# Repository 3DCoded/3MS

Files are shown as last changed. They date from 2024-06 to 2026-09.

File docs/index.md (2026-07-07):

---
title: 3MS Home
icon: material/home
---

# Welcome to the 3MS Documentation

The 3MS is short for MMMS, which stands for **M**odular **M**ulti **M**aterial **S**ystem

(https://www.printables.com/model/1108644-beta-3home-3ms-hybrid-official-modular-enclosure)

[Configuration Generator](https://forked-lined-hour.anvil.app/)

Discord Shield (https://discord.gg/ekqxDhdGCg)

The 3MS is a simple, compact, modular, reliable, budget-friendly multimaterial system.

[Get Started :material-format-list-numbered:](instructions/index.md){ .md-button }

## Why 3MS?

Why use the 3MS when there are many other multi-material systems?

Here are a few reasons:

- **Simplified Design**: Minimal mechanical complexity for increased reliability.
- **Low Cost**: A 4-filament-unit 3MS can be built for ~$150 USD
- **Easily Sourceable**: All the parts for the 3MS are available on Amazon. Alternatively, you can purchase a 3MS kit from West3D.
- **Comprehensive Documentation**: Step-by-step guides to ensure smooth setup and operation.
- **Scalable**: Easily expand the system to handle any number of filaments.

## Requirements

To use the 3MS, your setup should meet the following requirements:

- Run ^^legit^^ Klipper firmware. Most printers that come with Klipper preinstalled use a ^^modified^^ version of Klipper and/or Linux that will impact your ability to setup Happy Hare firmware. [Read more](https://klipper.discourse.group/t/3d-printers-with-preinstalled-and-modified-klipper-versions/20467?u=3dcoded)
- Have SSH (PuTTY) access (99.9% of Klipper installations have this, and if you don't you really should setup SSH).
- Have one spare USB port.
- Have an adapter to install a PTFE tube to the inlet of your printer's extruder.
- Have one filament sensor right before your printer's extruder.
- Have a filament cutter (ideally between your printer's extruder and hotend). Alternatively, you can use [IF-Cut](https://www.printables.com/model/1417085-beta-if-cut-inline-filament-cutter-for-the-3ms).

## Recommendations

It is recommended to install a filament cutter to your printer to avoid the need to tune tip forming.

## Get Started

To get started with the 3MS, see the [Master Instructions](instructions/index.md).

[Get Started :material-format-list-numbered:](instructions/index.md){ .md-button }

<iframe width="560" height="315"  src="https://www.youtube.com/embed/p-0RshsVmOk?si=rx554jrZFm6iZ0TR" title="YouTube video player" frameborder="0" allow="accelerometer; autoplay; clipboard-write; encrypted-media; gyroscope; picture-in-picture; web-share" referrerpolicy="strict-origin-when-cross-origin" allowfullscreen></iframe>

---

??? "Sample Prints"
    === "T-Rex"
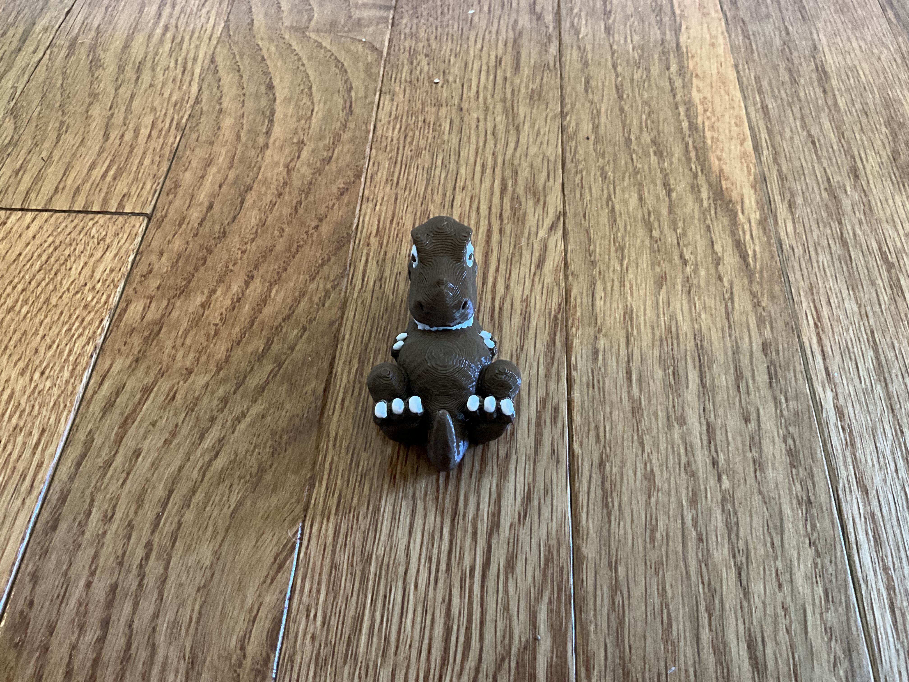
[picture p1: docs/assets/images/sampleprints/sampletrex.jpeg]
        

        Printed at 50% scale

        Model: [T-rex by Cipis](https://www.printables.com/model/5481-t-rex-multi-material)
    === "Lizard"
        

        Model: [Striped lizard with pupils by EngMike](https://www.printables.com/model/236193-striped-lizard-multi-material-with-pupils)
    === "Sheep"
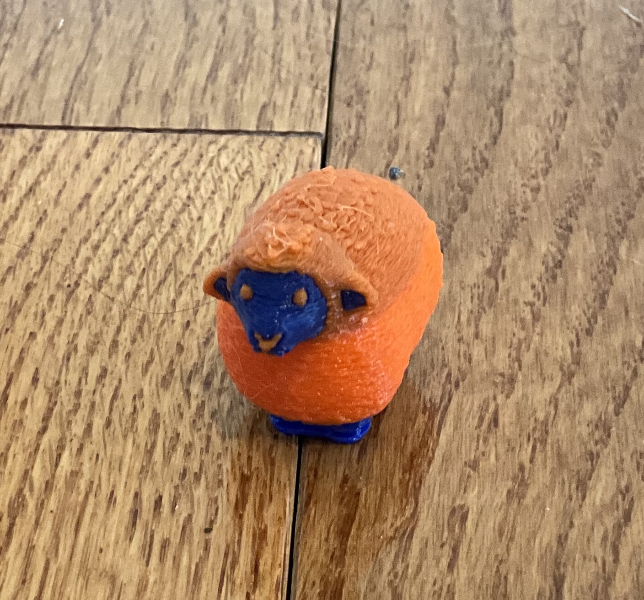
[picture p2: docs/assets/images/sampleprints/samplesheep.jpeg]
        

        Model: [Sheep by Cipis](https://www.printables.com/model/838872-sheep-multi-material-remix)
    === "Calendar"
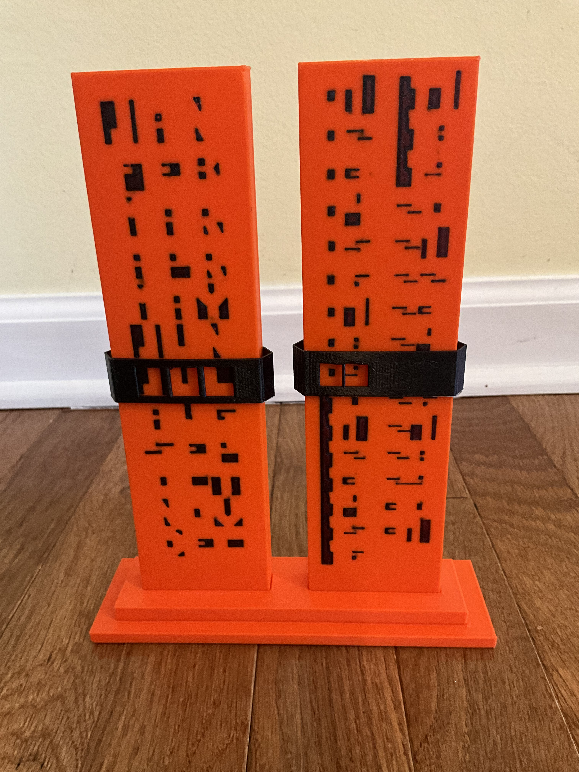
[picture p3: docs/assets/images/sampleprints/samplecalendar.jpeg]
        

        Model: [Monolith Cryptic Calendar by Sevro](https://www.printables.com/model/698341-monolith-cryptic-calendar)
    === "Voron Cube"
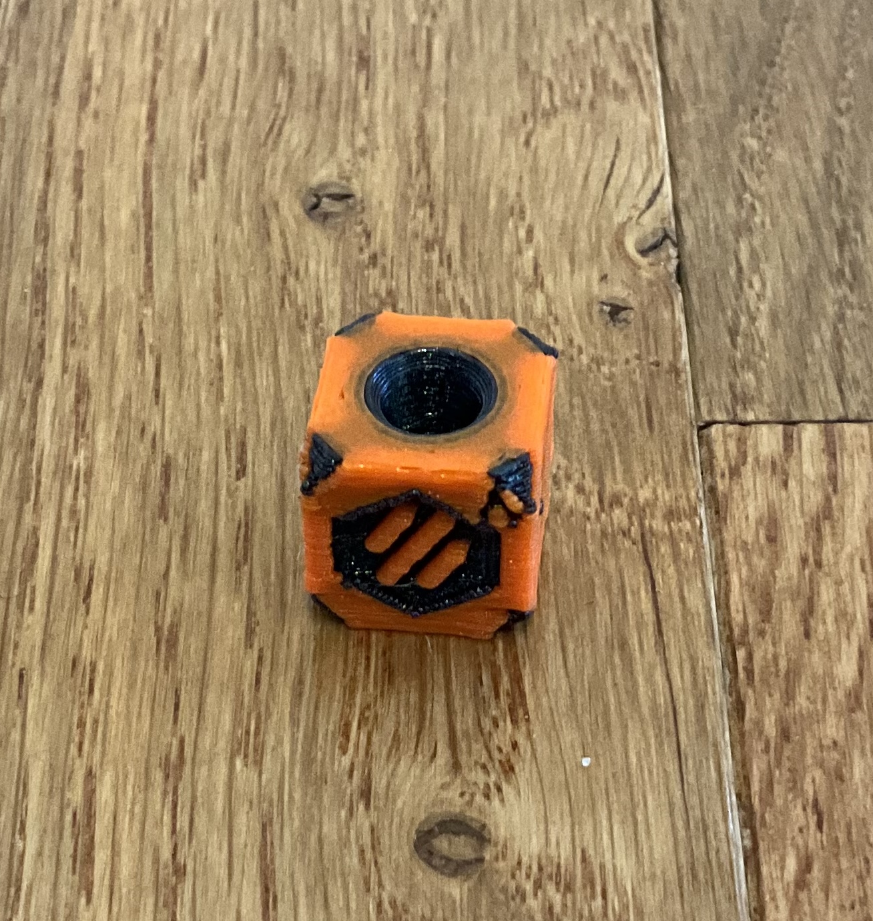
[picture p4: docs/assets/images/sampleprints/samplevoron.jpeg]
        

        Model: Voron Cube (bundled with OrcaSlicer), painted by me in OrcaSlicer

??? "West3D Video Series"
    Thank you to Allen Rowand from [West3D](https://west3d.com/) for making this ongoing series on the 3MS.

    <iframe width="560" height="315" src="https://www.youtube.com/embed/XfjHtymdHao?si=cHG1jreb8FfjpWaL" title="YouTube video player" frameborder="0" allow="accelerometer; autoplay; clipboard-write; encrypted-media; gyroscope; picture-in-picture; web-share" referrerpolicy="strict-origin-when-cross-origin" allowfullscreen></iframe>

    <iframe width="560" height="315" src="https://www.youtube.com/embed/o4Fvtdl-XjM?si=16Prr2Djn4XP0n6q" title="YouTube video player" frameborder="0" allow="accelerometer; autoplay; clipboard-write; encrypted-media; gyroscope; picture-in-picture; web-share" referrerpolicy="strict-origin-when-cross-origin" allowfullscreen></iframe>

    <iframe width="560" height="315" src="https://www.youtube.com/embed/Ndw14nttqQs?si=JtjTmIGCPrT_j4LV" title="YouTube video player" frameborder="0" allow="accelerometer; autoplay; clipboard-write; encrypted-media; gyroscope; picture-in-picture; web-share" referrerpolicy="strict-origin-when-cross-origin" allowfullscreen></iframe>

    <iframe width="560" height="315" src="https://www.youtube.com/embed/UaJ6kVc53ME?si=NVuBHkkHWb-64-Eb" title="YouTube video player" frameborder="0" allow="accelerometer; autoplay; clipboard-write; encrypted-media; gyroscope; picture-in-picture; web-share" referrerpolicy="strict-origin-when-cross-origin" allowfullscreen></iframe>

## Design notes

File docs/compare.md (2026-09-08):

---
icon: material/select-compare
description: Comparison of various Klipper multimaterial systems, including 3MS, ERCF, BoxTurtle, Tradrack, Pico, QuattroBox, EMU, NightOwl, CoPrint, MMX
comments: true
---

# Comparison of Multimaterial Systems

Not sure if you want to use the 3MS? Check this comparison between several common multimaterial systems.

<div class="grid cards" markdown>
-   3MS __Modular Multimaterial System for Klipper 3D Printers__

    --- 

    

    ---

    **Pros:**

    :material-plus-box:{.plus} Simple Design

    :material-plus-box:{.plus} Reliability

    :material-plus-box:{.plus} Documentation

    :material-plus-box:{.plus} Modular Design

    :material-plus-box:{.plus} Active Community

    :material-plus-box:{.plus} Price (~$150)

    ---

    **Cons:**

    :material-minus-box:{.minus} Compatibility (only Klipper)

</div>

<div class="grid cards" markdown>

-   Box Turtle MMU __Automated Filament Changer__

    ---

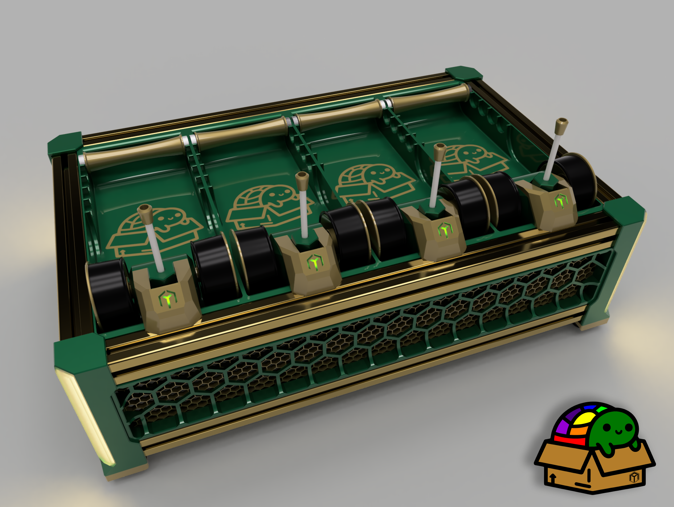
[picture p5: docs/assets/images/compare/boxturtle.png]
    

    ---

    **Pros:**

    :material-plus-box:{.plus} Reliability

    :material-plus-box:{.plus} Active Community

    :material-plus-box:{.plus} Documentation

    ---

    **Cons:**

    :material-minus-box:{.minus} Compatibility (only Klipper)
    
    :material-minus-box:{.minus} Complexity

    :material-minus-box:{.minus} Price ($300)

- QuattroBox __Filamentalist-Based MMU__

    ---

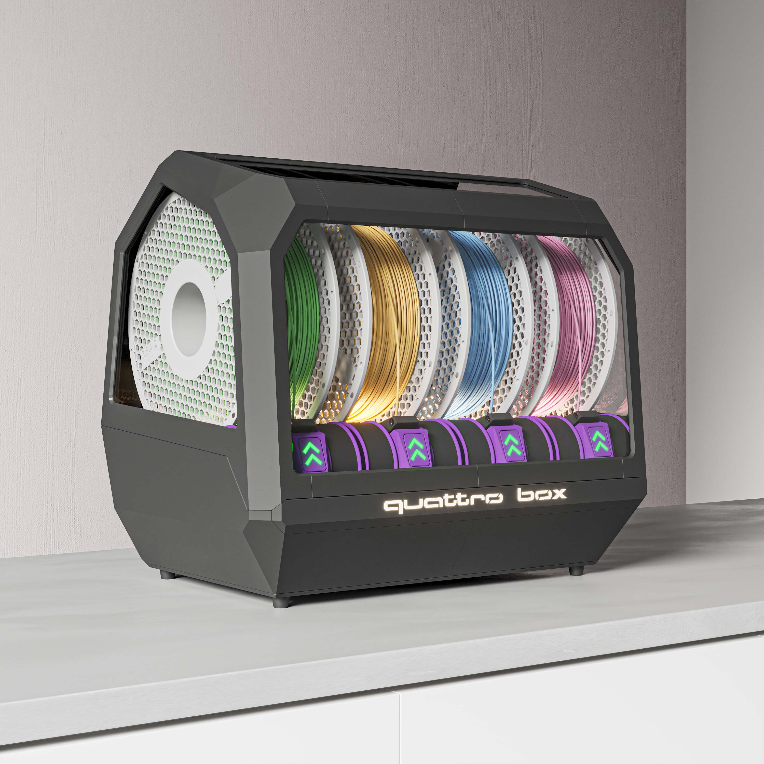
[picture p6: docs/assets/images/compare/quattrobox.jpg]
    

    ---

    **Pros:**

    :material-plus-box:{.plus} Reliability

    :material-plus-box:{.plus} Passive Rewinders

    :material-plus-box:{.plus} Aesthetics

    **Cons:**

    :material-minus-box:{.minus} Compatibility (only Klipper)

    :material-minus-box:{.minus} Complexity

    :material-minus-box:{.minus} Price

- NightOwl __Integrated Dual Spool Filament Switching System__

    ---

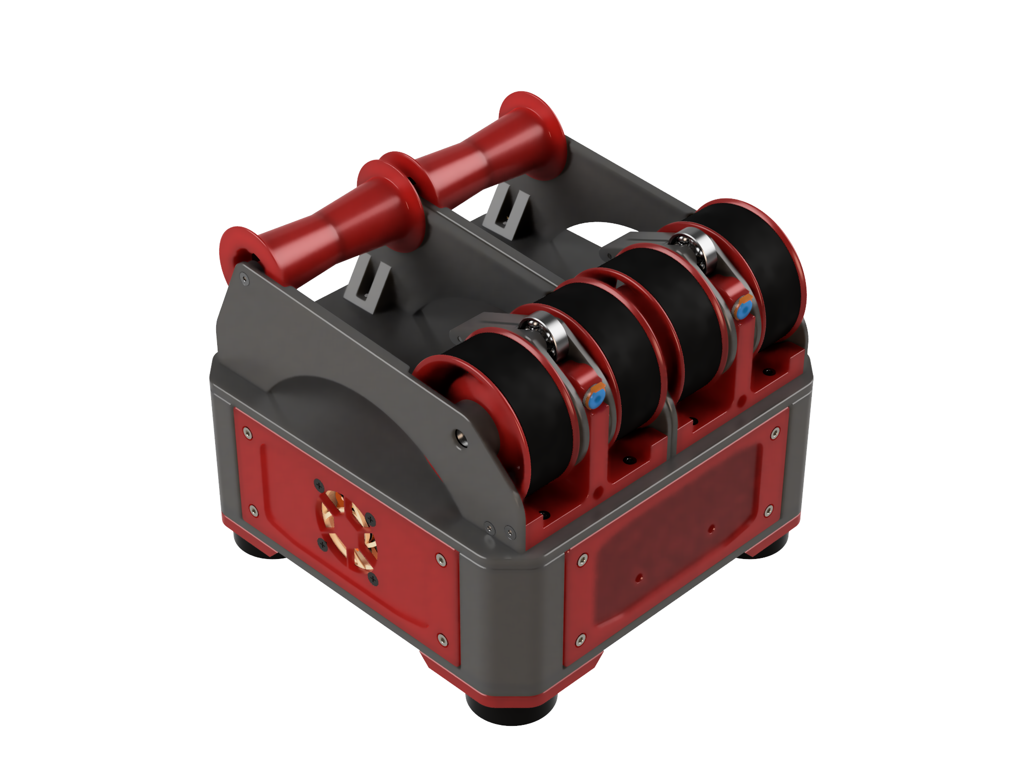
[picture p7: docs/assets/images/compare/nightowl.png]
    

    ---

    **Pros:**

    :material-plus-box:{.plus} Reliability

    :material-plus-box:{.plus} Simple Design

    :material-plus-box:{.plus} Compact Design

    **Cons:**

    :material-minus-box:{.minus} Expandability (only 2 spools)

    :material-minus-box:{.minus} Compability (only Klipper)

-   ERCF v2 __An expandable MMU for Klipper-based 3D-printers__

    ---

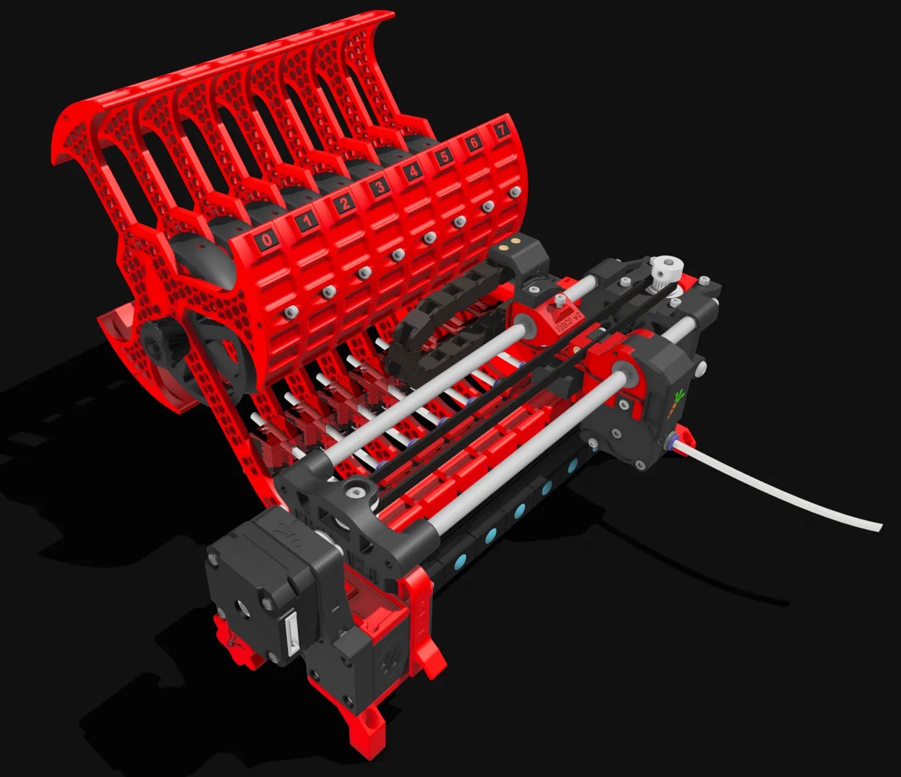
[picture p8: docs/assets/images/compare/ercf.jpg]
    

    ---

    **Pros:**

    :material-plus-box:{.plus} Reliability

    :material-plus-box:{.plus} Modular Design

    :material-plus-box:{.plus} Active Community

    :material-plus-box:{.plus} Documentation

    ---

    **Cons:**

    :material-minus-box:{.minus} Compatibility (only Klipper)

    :material-minus-box:{.minus} Complexity

-   TradRack __by Annex Engineering__

    ---

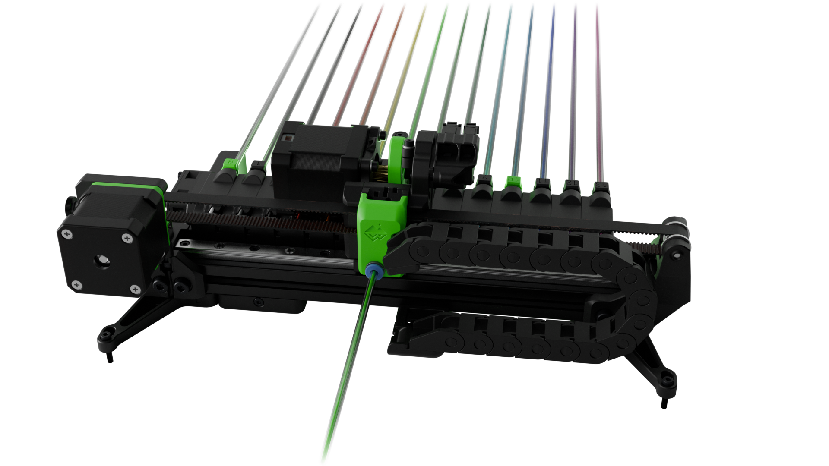
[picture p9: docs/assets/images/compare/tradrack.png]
    

    ---

    **Pros:**

    :material-plus-box:{.plus} Reliability

    :material-plus-box:{.plus} Modular Design

    :material-plus-box:{.plus} Active Community

    :material-plus-box:{.plus} Documentation

    ---

    **Cons:**

    :material-minus-box:{.minus} Compatibility (only Klipper)

    :material-minus-box:{.minus} Complexity

- Pico MMU __Open-source project designed to enable multi-material 3D printing on FDM printers__

    ---

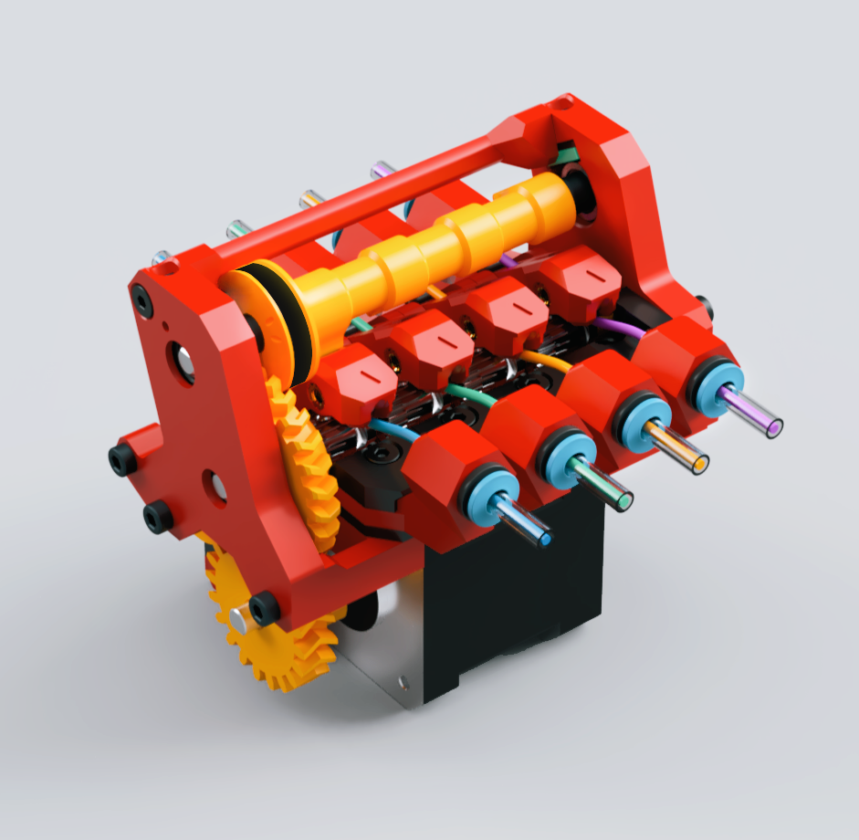
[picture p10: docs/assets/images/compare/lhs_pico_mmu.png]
    

    ---

    **Pros:**

    :material-plus-box:{.plus} Simple Design

    :material-plus-box:{.plus} Compact Design

    :material-plus-box:{.plus} Speed

    ---

    **Cons:**

    :material-minus-box:{.minus} Compatibility (only Klipper)

    :material-minus-box:{.minus} Reliability

- MMX __Multi-Material Extruder__

    ---

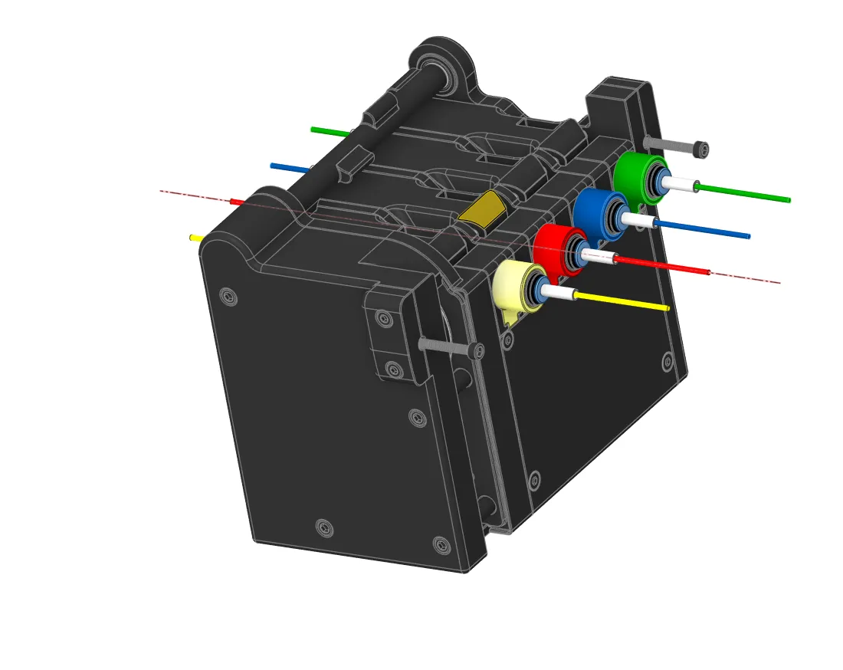
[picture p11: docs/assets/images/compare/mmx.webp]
    

    ---

    **Pros:**

    :material-plus-box:{.plus} Simple Design

    :material-plus-box:{.plus} Compact Design

    :material-plus-box:{.plus} Speed

    ---

    **Cons:**

    :material-minus-box:{.minus} Compatibility (only Klipper)

    :material-minus-box:{.minus} Reliability

-   3DChameleon MK4 __Automatic Color Changer__

    ---

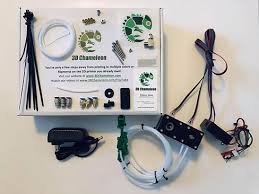
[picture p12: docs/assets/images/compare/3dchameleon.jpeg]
    

    ---

    **Pros:**

    :material-plus-box:{.plus} Compatibility

    :material-plus-box:{.plus} No custom firmware

    :material-plus-box:{.plus} Price ($200)

    ---

    **Cons:**

    :material-minus-box:{.minus} Reliability
    
    :material-minus-box:{.minus} Documentation

- SMuFF __Smart Multi Filament Feeder__

    ---

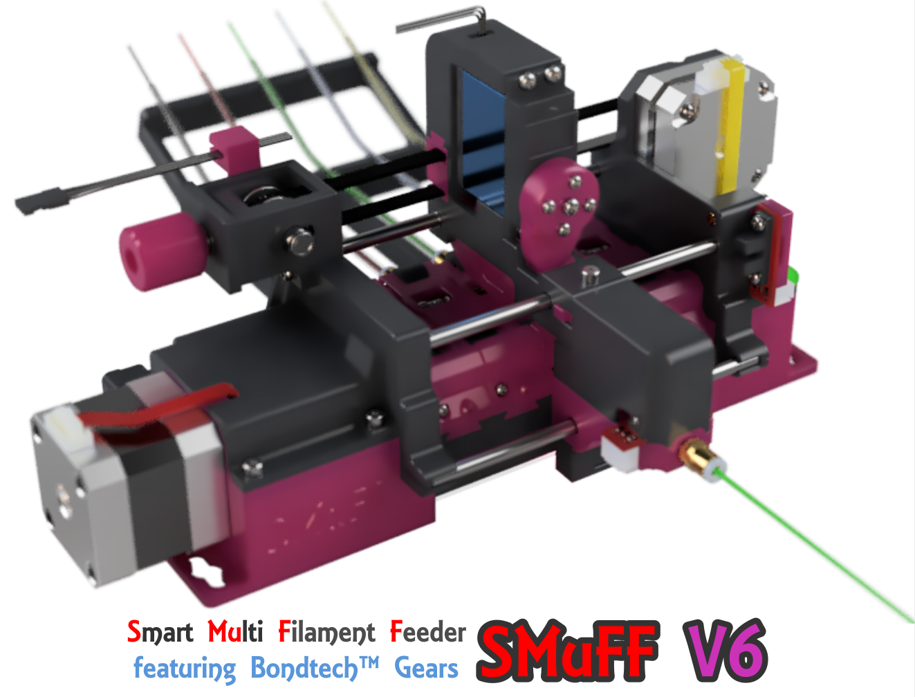
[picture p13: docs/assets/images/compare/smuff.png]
    
    
    ---

    **Pros:**

    :material-plus-box:{.plus} Reliability

    :material-plus-box:{.plus} Modular Design

    :material-plus-box:{.plus} Documentation

    ---

    **Cons:**

    :material-minus-box:{.minus} Complexity

-   Prusa MMU3 __Multi Material Upgrade__

    ---

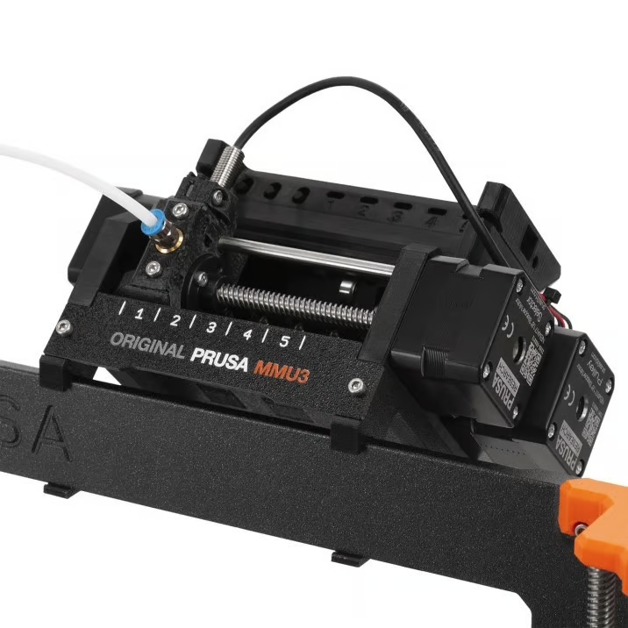
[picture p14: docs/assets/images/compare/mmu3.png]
    

    ---

    **Pros:**

    :material-plus-box:{.plus} Reliability

    :material-plus-box:{.plus} Support

    :material-plus-box:{.plus} Documentation

    ---

    **Cons:**

    :material-minus-box:{.minus} Compatibility

    :material-minus-box:{.minus} Price ($300)

-   CoPrint KCM __Multi-Color Upgrade Kit for Klipper 3D Printers__

    ---

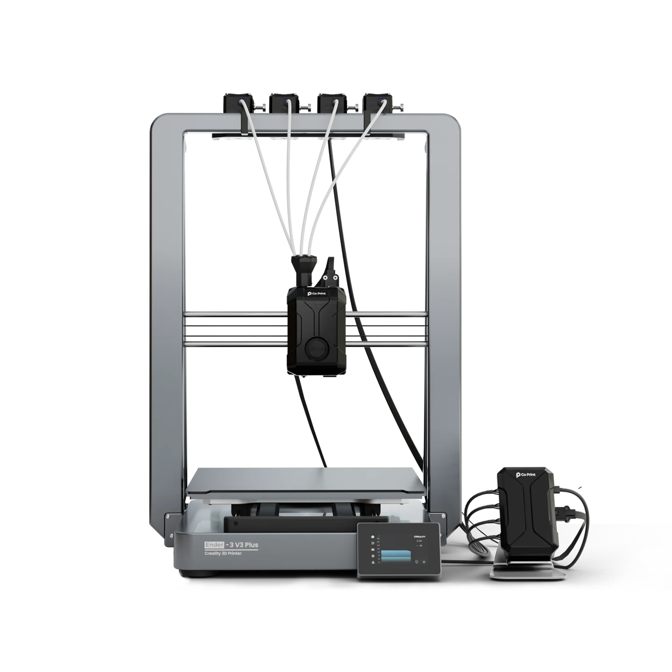
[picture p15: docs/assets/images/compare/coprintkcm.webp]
    

    ---

    **Pros:**

    :material-plus-box:{.plus} Simple Design

    :material-plus-box:{.plus} Modular Design

    :material-plus-box:{.plus} Documentation

    ---

    **Cons:**

    :material-minus-box:{.minus} Complexity (relies on ChromaHead)

    :material-minus-box:{.minus} Price (~$300)

</div>

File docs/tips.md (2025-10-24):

---
comments: true
icon: material/lightbulb-on
---

# Tips / FAQ

## Which board should I use?

The recommended board for the 3MS is the SKR Pico due to its compact size, reliability, and cost-effectiveness.

## What sensors do I need?

To use the 3MS, you need a sensor between the exit of the Y-splitter and your printer's extruder. If it's closer to the Y-splitter, it's considered a shared gate sensor while if it's closer to the extruder it's called an extruder entry sensor.

## Do I need a filament cutter?

Using a filament cutter is recommended as it takes a lot of the guesswork out of tuning tip forming. A quick Google search of "filament cutter for [MY PRINTER]" is usually good to find a filament cutter for your printer.

You can find user-submitted tip cutting/forming configurations [here](https://link.3dcoded.xyz/tipconfigs/).

If there isn't a filament cutter published for your printer, you have two options:

- Design your own

- Tune tip forming

The latter option may seem easier at first, but tip forming isn't as straightforward as you might think.

Here are a few general tips:

- If your tips come out stringy, use more cooling moves and a lower temperature. Also, skinnydip string reduction can help here.
- If your tips come out with a larger tip, use less cooling moves and a higher temperature.
- Use Happy Hare's [`_MMU_FORM_TIP`](https://github.com/moggieuk/Happy-Hare/wiki/Tip-Forming-and-Purging#tuning-happy-hare-_mmu_form_tip-macro) macro to help tune your tips.

## Why isn't `MMU_LOAD`/`MMU_UNLOAD` loading/unload the filament enough?

Run the below command in Mainsail/Fluidd:

```
MMU_STATUS DETAIL=1 SHOWCONFIG=1
```

The output will show exactly what Happy Hare does on load and unload. You can look at the referenced parameters (editable in `mmu_parameters.cfg`) and adjust as necessary to get your load/unload just right.

## More Tips / FAQ's always welcome!

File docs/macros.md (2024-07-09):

# Macros

## MMMS Settings

### MMMS_SETTINGS
Stores the settings settings for the 3MS.

**Default Settings**

```
variable_load_distance: 210
variable_unload_distance: 200
variable_load_speed: 4500
vairable_unload_speed: 4500
variable_num_tools: 2
```

**Example Usage**

```
MMMS_SETTINGS
```

### SET_MMMS_SETTINGS
Sets the configuration for the 3MS. Allows **temporary** customization of load and unload distances and speeds

**Example Usage**

```
SET_MMMS_SETTINGS LOAD_DISTANCE=210 UNLOAD_DISTANCE=200 LOAD_SPEED=3500 UNLOAD_SPEED=5500
```

## Filament Handling

### MMMS_UNLOAD
Unloads filament by a specified distance and speed. If no distance/speed is specified, it uses the default unload distance/speed from `MMMS_SETTINGS`.

**Example Usage**

```
MMMS_UNLOAD DISTANCE=200 SPEED=5500
```

### MMMS_LOAD
Loads filament by a specified distance and speed. If no distance/speed is specified, it uses the default load distance/speed from `MMMS_SETTINGS`.

**Example Usage**

```
MMMS_LOAD DISTANCE=210 SPEED=3500
```

### CHECK_FSENSOR
Checks the filament sensor state. Pauses the print if the sensor state does not match the expected value.

**Example Usage**

```
CHECK_FSENSOR V=1
```

## Tool Sync

### SET_TOOL_SYNC
Sets the sync state of a tool. Syncs or desyncs the specified tool to/from the extruder.

**Example Usage**

```
SET_TOOL_SYNC TOOL=0 SYNC=1
```

### SYNC_TOOL
Syncs the specified tool and desyncs all other tools to/from the extruder.

**Example Usage**

```
SYNC_TOOL TOOL=0
```

### DESYNC_TOOL
Desyncs the specified tool from the extruder.

**Example Usage**

```
DESYNC_TOOL TOOL=0
```

### CLEAR_TOOL
Clears the current tool selection by setting it to -1.

**Example Usage**

```
CLEAR_TOOL
```

### DESYNC_ALL_TOOLS
Desyncs all configured tools.

**Example Usage**

```
DESYNC_ALL_TOOLS
```

## Print Start and End

### MMMS_START
Starts the print by checking the filament sensor. If filament is detected, the print is paused and the user is notified. Regardless of the filament sensor state, the initial tool is loaded.

**Example Usage**

```
MMMS_START INITIAL_TOOL=0
```

### MMMS_END
Ends the print by unloading the current tool. If filament is detected after unloading, the user is notified.

**Example Usage**

```
MMMS_END
```

## Tool Change

### T0
Changes to tool 0.

**Example Usage**

```
T0
```

### T1
Changes to tool 1.

**Example Usage**

```
T1
```

### Tx
Changes to a specified tool. Replace `x` with the tool number.

**Example Usage**

```
T2
T3
```

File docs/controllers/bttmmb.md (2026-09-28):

---
comments: true
---

# BTT MMB V1

**Max filament units: 4**

**MCU Name: `mmu`**

## BOM

| Name | Price | Quantity | Link | Notes |
| - | - | - | - | - |
| BTT MMB | $34.99 | 1 | [BTT](https://biqu.equipment/products/bigtreetech-mmb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) | |
22AWG Cable | $9.99 | 1 | [Amazon](https://a.co/d/0oP9cD3) | These wires are only sufficient to run steppers, not heaters |
| 24V PSU | $7.39 | 1 | Amazon | This PSU is only sufficient to run steppers, not heaters |

{{ filUnitBOM }}

## Wiring

Route the wires from the NEMA17's to the controller board. Follow this table to determine which port to plug the motors into:

| Filament Unit # | Motor Port |
| - | - |
| 0 | M1 |
| 1 | M2 |
| 2 | M3 |
| 3 | M4 |

Now, grab your 24V PSU and two M-M duponts, one red and one black (M-M means that there is metal coming out of both ends of the cable). Plug the PSU into the wall, but don't plug the screw terminals into the PSU (the screw terminals have green)

1. Plug the red wire into the positive terminal of the screw terminals
2. Plug the black wire into the negative terminal of the screw terminals

    !!! danger
        These dupont cables are too thin to run much more than the stepper motors. If you run a heater or other power-intensive device off of the MMB board, the duponts and/or PSU can melt/catch fire. To reduce the risk of this, you can double up on the duponts or get thicker wires.

3. Following this image, locate the HVIN and GND inputs (top left)

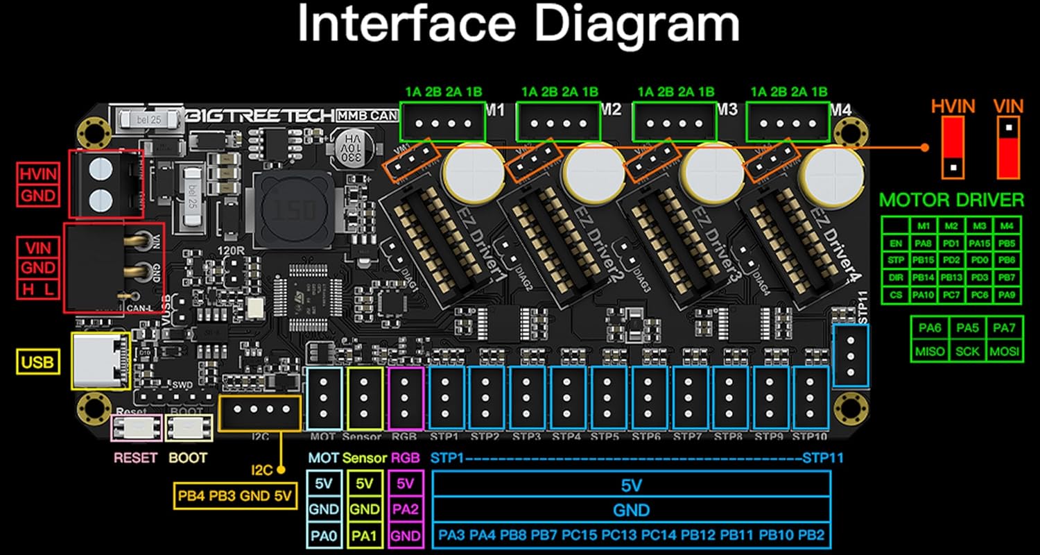
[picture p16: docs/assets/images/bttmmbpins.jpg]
    

4. Route the two wires inside closest to the HVIN and GND inputs
5. Using the markings on the board, plug the red wire into the HVIN terminal on the MMB
6. Using the markings on the board, plug the black wire into the GND terminal on the MMB

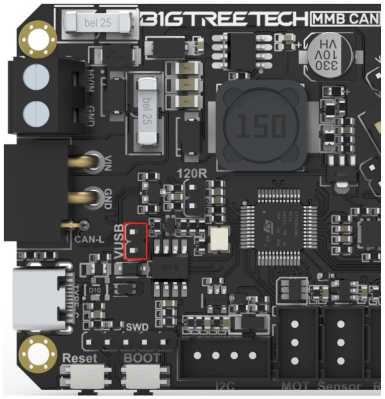
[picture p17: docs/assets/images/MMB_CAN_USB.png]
    

7. Install the VUSB jumper.

    !!! tip
        After you've flashed firmware, remove the VUSB jumper.

7. Verify all connections

    !!! warning
        If the wires are plugged into the wrong place, or swapped polarities, your MMB, Stepper motors, and/or PSU can be badly damaged.

8. Plug the PSU screw terminals into the PSU wire

Plug the MMB into your Klipper host with the cable that came with it.

If the MMB lights up, you wired it correctly!

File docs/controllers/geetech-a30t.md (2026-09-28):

---
comments: true
---

# Geetech A30T

**Contributed by [@ImChrono](https://github.com/ImChrono)**

---

**Max filament units: 7**

**MCU Name: `3ms`**

## BOM

| Name | Price | Quantity | Link | Notes |
| - | - | - | - | - |
| Geetech A30T | $34.99 | 1 | [Geetech](https://www.geeetech.com/a30t-printer-gtm32103v1-control-board-p-1190.html) | |
22AWG Cables | $9.99 | 1 | [Amazon](https://a.co/d/0oP9cD3) | These wires are only sufficient to run steppers, not heaters |
| 24V PSU | $7.39 | 1 | [Amazon](https://a.co/d/1Ko6QMB) | This PSU is only sufficient to run steppers, not heaters |

{{ filUnitBOM }}

## Firmware

To flash Klipper firmware to the A30T, run the following command and see the following screenshot:

```sh
cd ~/klipper
make menuconfig
```

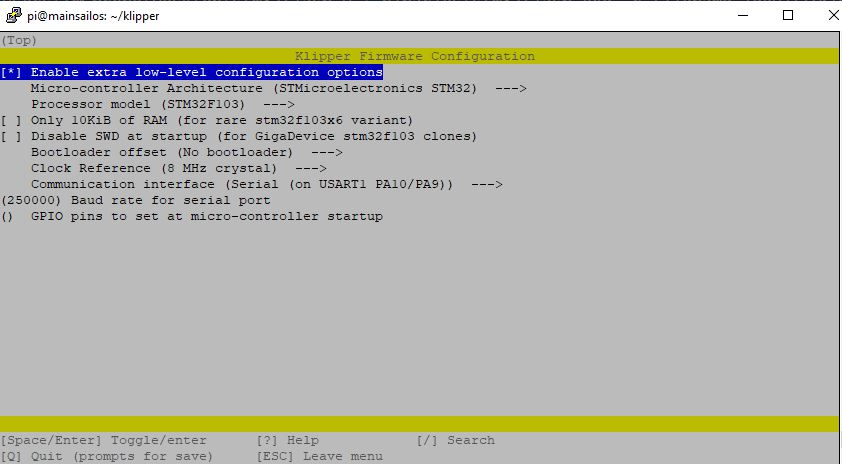
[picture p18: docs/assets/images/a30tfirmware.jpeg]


Next, connect the **BOOT0** jumper on the A30T and run:

```sh
stm32flash -i ',,,,,' -v -w out/klipper.bin -g 0 /dev/serial/by-id/<your-mcu-id-here>
```

## Wiring

Route the wires from the NEMA17's to the controller board. Follow this table to determine which port to plug the motors into:

| Filament Unit # | Motor Port |
| - | - |
| 0 | X |
| 1 | Y |
| 2 | Z0 |
| 3 | Z1 |
| 4 | E1 |
| 5 | E2 |
| 6 | E3 |

Now, grab your 12V PSU and two M-M duponts, one red and one black (M-M means that there is metal coming out of both ends of the cable). Plug the PSU into the wall, but don't plug the screw terminals into the PSU (the screw terminals have green)

1. Plug two red wires into the positive terminal of the screw terminals
2. Plug two black wires into the negative terminal of the screw terminals

    !!! danger
        These dupont cables are too thin to run much more than the stepper motors. If you run a heater or other power-intensive device off of the motherboard, the duponts and/or PSU can melt/catch fire. To reduce the risk of this, you can double up on the duponts or get thicker wires.

4. Route the four wires inside closest to your chosen input
5. Using the markings on the board, plug the two red wires into the positive terminal on the motherboard
6. Using the markings on the board, plug the two black wires into the negative terminal on the motherboard
7. Verify all connections

    !!! warning
        If the wires are plugged into the wrong place, or swapped polarities, your motherboard, Stepper motors, and/or PSU can be badly damaged.

8. Plug the PSU screw terminals into the PSU wire

If the motherboard lights up, you wired it correctly!

Finally, plug the motherboard into your Klipper host with the cable that came with it.

---

## UART Conversion

### ⚠️ Attention: Proceed with Caution! ⚠️
This modification involves delicate hardware changes that require precision and attention to detail. Mistakes in wiring or soldering can permanently damage your **GTM32_103_V1 board**. 

- **Double-check connections** before applying power.
- Use proper tools and follow best practices for soldering.
- If you are not confident in your skills, seek assistance from an experienced individual or professional.

**You proceed at your own risk.**

### Overview
This guide details the process of modifying the **GTM32_103_V1** 3D printer controller board to enable UART capabilities. The GTM32_103_V1 board features 7 **TMC2208 drivers** operating in standalone mode by default. This modification involves **removing the SD card slot** and repurposing its pinouts for UART communication.

---

### Features of the Modification

- **UART Capability**: Enables communication with TMC2208 drivers via UART repurposing the SDCard slot

---

### Hardware Changes

#### Components Modified
- **SD Card Slot**: Removed entirely to free up pinouts for UART.
- **Repurposed Pins**: SD card slot pins are reassigned as per the following table:

| TCM2208 Driver | SD Card Pin | STM32 Pin |
|---|---|---|
| Motor0 | 9 | PC7 |
| Motor1 | 8 | PC9 |
| Motor2 | 7 | PC8 |
| Motor3 | 5 | PC12 |
| Motor4 | 3 | PD2 |
| Motor5 | 2 | PC11 |
| Motor6 | 1 | PC10 |

#### Procedure
1. **Remove Pull down resistor from each driver**:
   - Desolder the SMD 1kΩ resistor carefully to avoid damaging the surrounding components.

| TMCDriver | PCB Code |
|---|---|
| Motor0 | R53 |
| Motor1 | R57 |
| Motor2 | R62 |
| Motor3 | R120 |
| Motor4 | R71 |
| Motor5 | R95 |
| Motor6 | R105 |

2. **Remove the SD Card Slot**:
   - Desolder the SD card slot carefully to avoid damaging the surrounding components.
3. **Repurpose the Pinouts**:
   - Rewire the SD card pins according to the table above.
   - Connect each pin to its corresponding UART connection for the TMC2208 drivers.

---

### Testing and Validation
After completing the hardware changes:
1. Connect the board to your 3D printer and power it on.
2. Use your firmware to verify UART communication with each TMC2208 driver.
3. Check for successful responses from the drivers using a terminal or debugging tool.

---

### Photos

- Close-up of the TMC driver
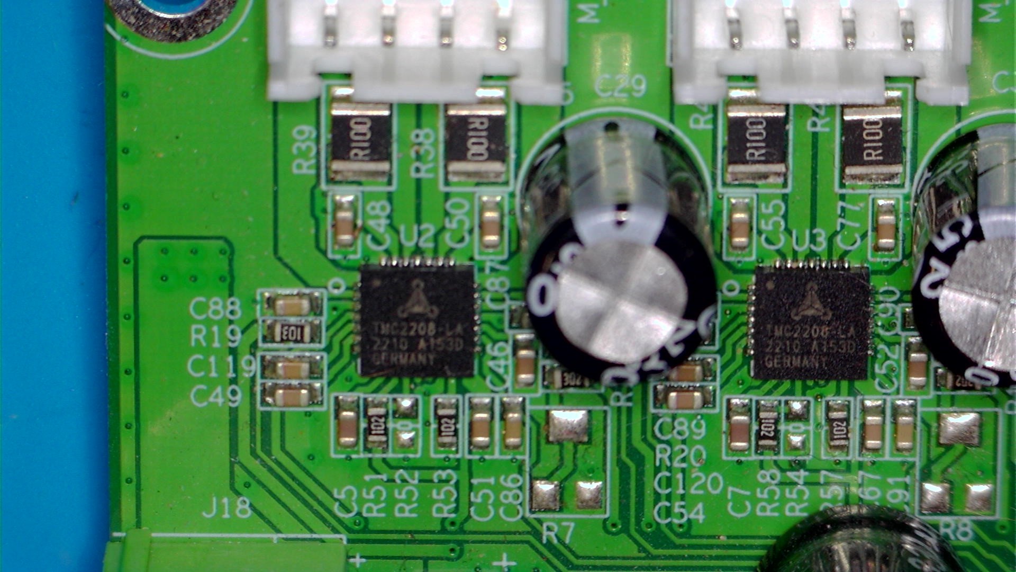
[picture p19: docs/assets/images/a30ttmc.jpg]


- Close-up of the TMC driver with resistor removed (solder the uart pint to the red signed pin)
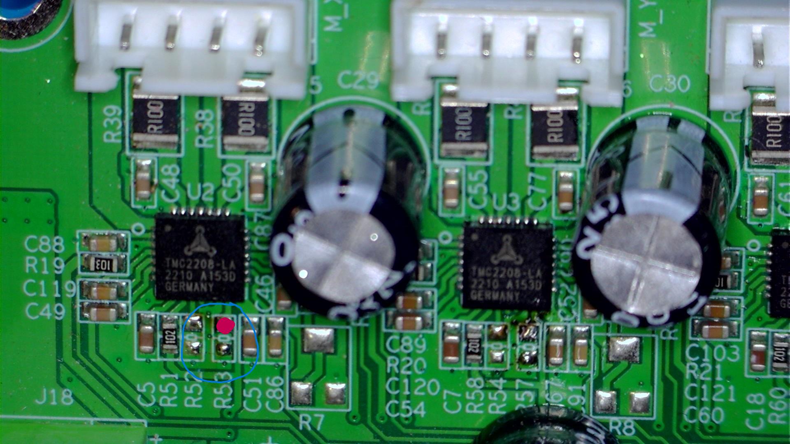
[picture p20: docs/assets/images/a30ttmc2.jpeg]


- Close-up of the SD card:
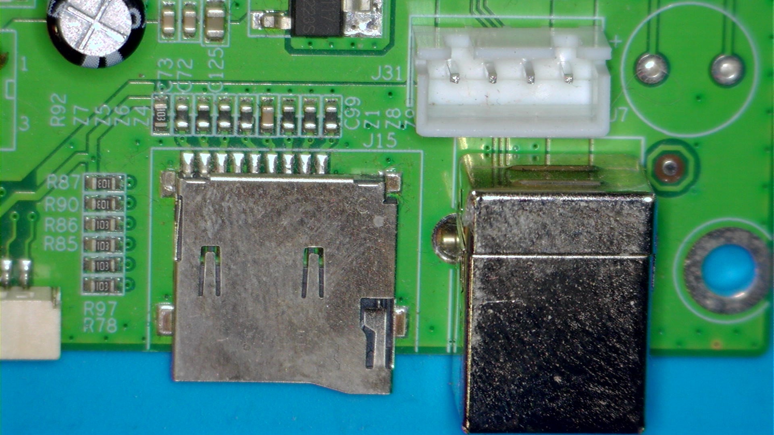
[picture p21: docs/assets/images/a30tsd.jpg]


- Rewired pins with labels.
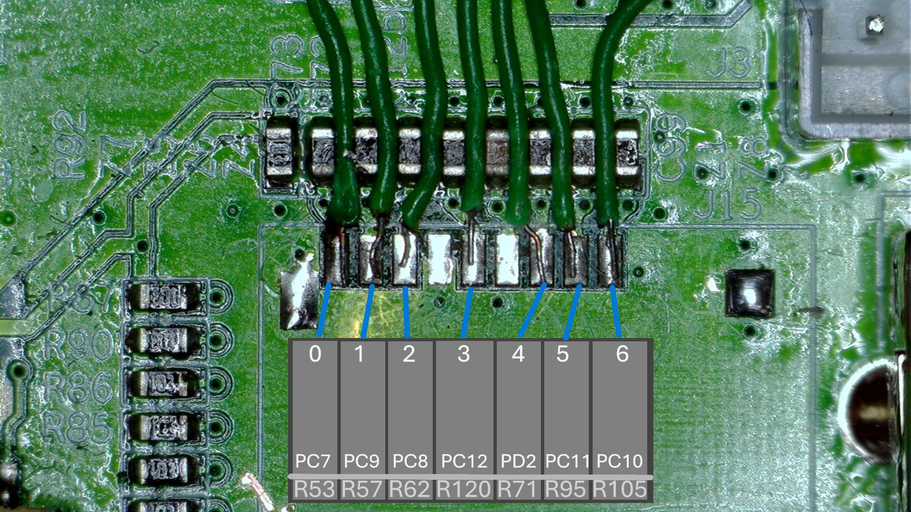
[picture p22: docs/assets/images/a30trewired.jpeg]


---

### UART Configuration

When configuring this board with Happy Hare firmware, be sure to use `UART-mmu.cfg` and `UART-mmu_hardware.cfg` (renaming to `mmu.cfg` and `mmu_hardware.cfg` respectively).

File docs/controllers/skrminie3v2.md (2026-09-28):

---
comments: true
---

# BTT SKR Mini E3 V2

**Max filament units: 4**

**MCU Name: `3ms`**

## BOM

| Name | Price | Quantity | Link | Notes |
| - | - | - | - | - |
| SKR Mini E3 V2 | $34.99 | 1 | [Amazon](https://a.co/d/0hgHU9JX) | |
22AWG Cables | $9.99 | 1 | [Amazon](https://a.co/d/0oP9cD3) | These wires are only sufficient to run steppers, not heaters |
| 12V PSU | $7.39 | 1 | [Amazon](https://a.co/d/0Zninyc) | This PSU is only sufficient to run steppers, not heaters |

{{ filUnitBOM }}

## Wiring

Route the wires from the NEMA17's to the controller board. Follow this table to determine which port to plug the motors into:

| Filament Unit # | Motor Port |
| - | - |
| 0 | XM |
| 1 | YM |
| 2 | ZAM or ZBM |
| 3 | E0M |

Now, grab your 12V PSU and two M-M duponts, one red and one black (M-M means that there is metal coming out of both ends of the cable). Plug the PSU into the wall, but don't plug the screw terminals into the PSU (the screw terminals have green)

1. Plug the red wire into the positive terminal of the screw terminals
2. Plug the black wire into the negative terminal of the screw terminals

    !!! danger
        These dupont cables are too thin to run much more than the stepper motors. If you run a heater or other power-intensive device off of the SKR board, the duponts and/or PSU can melt/catch fire. To reduce the risk of this, you can double up on the duponts or get thicker wires.

3. Following this image, choose either the DCIN or POWER input
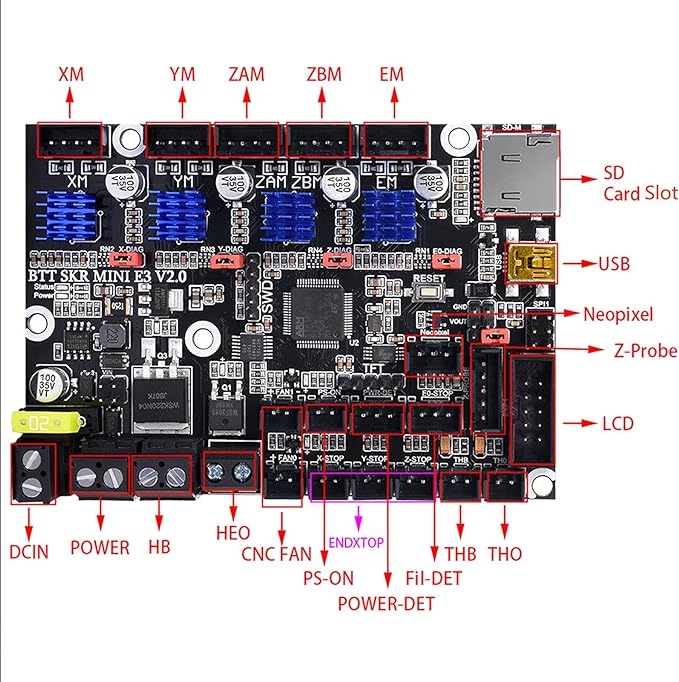
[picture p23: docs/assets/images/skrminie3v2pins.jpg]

4. Route the two wires inside closest to your chosen input
5. Using the markings on the board, plug the red wire into the positive terminal on the SKR
6. Using the markings on the board, plug the black wire into the negative terminal on the SKR
7. Verify all connections

    !!! warning
        If the wires are plugged into the wrong place, or swapped polarities, your SKR, Stepper motors, and/or PSU can be badly damaged.

8. Plug the PSU screw terminals into the PSU wire

If the SKR lights up, you wired it correctly!

Finally, plug the SKR into your Klipper host with the blue cable that came with it.

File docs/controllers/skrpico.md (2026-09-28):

---
icon: material/check
comments: true
---

# BTT SKR Pico

<!-- **Max filament units: 4**

**MCU Name: `mmu`**

## BOM

| Name | Price | Quantity | Link | Notes |
| - | - | - | - | - |
| SKR Pico | $26.58 | 1 | [BIQU](https://biqu.equipment/products/btt-skr-pico-v1-0?variant=40565262155874) | |
24AWG Power Cables | $9.99 | 1 | [Amazon](https://a.co/d/5iee9KD) | These wires are only sufficient to run steppers, not heaters |
| 24V PSU | $12.98 | 1 | [Amazon](https://a.co/d/6BJT2RP) | This PSU is only sufficient to run steppers, not heaters |

{{ filUnitBOM }}

## Wiring

Route the wires from the NEMA17's to the controller board. Follow this table to determine which port to plug the motors into:

| Filament Unit # | Motor Port |
| - | - |
| 0 | X |
| 1 | Y |
| 2 | Z1 or Z2 |
| 3 | E |

Now, grab your 24V PSU and two M-M duponts, one red and one black (M-M means that there is metal coming out of both ends of the cable). Plug the PSU into the wall, but don't plug the screw terminals into the PSU (the screw terminals have green)

1. Plug the red wire into the positive terminal of the screw terminals
2. Plug the black wire into the negative terminal of the screw terminals

    !!! danger
        These dupont cables are too thin to run much more than the stepper motors. If you run a heater or other power-intensive device off of the SKR board, the duponts and/or PSU can melt/catch fire. To reduce the risk of this, you can double up on the duponts or get thicker wires.

3. Following this image, locate the POWER input
![](skrpicopins.png)
4. Route the two wires inside closest to the POWER input
5. Using the markings on the board, plug the red wire into the positive terminal on the SKR
6. Using the markings on the board, plug the black wire into the negative terminal on the SKR
7. Verify all connections

    !!! warning
        If the wires are plugged into the wrong place, or swapped polarities, your SKR, Stepper motors, and/or PSU can be badly damaged.

8. Plug the PSU screw terminals into the PSU wire

If the SKR lights up, you wired it correctly!

Finally, plug the SKR into your Klipper host with the blue cable that came with it. -->

## Firmware Installation

Setting up firmware for the SKR Pico can be divided into four major steps:

1. Compile Katapult (bootloader)
2. Flash Katapult
3. Compile Klipper
4. Flash Klipper

### Compiling Katapult

You have two options for installing Katapult to the SKR Pico:

=== "1. Compile Katapult yourself"
    Run the following commands in SSH:

    ```
    cd ~/
    git clone https://github.com/Arksine/katapult
    cd katapult
    make menuconfig
    ```

    Adjust your `menuconfig` parameters to match the following exactly.

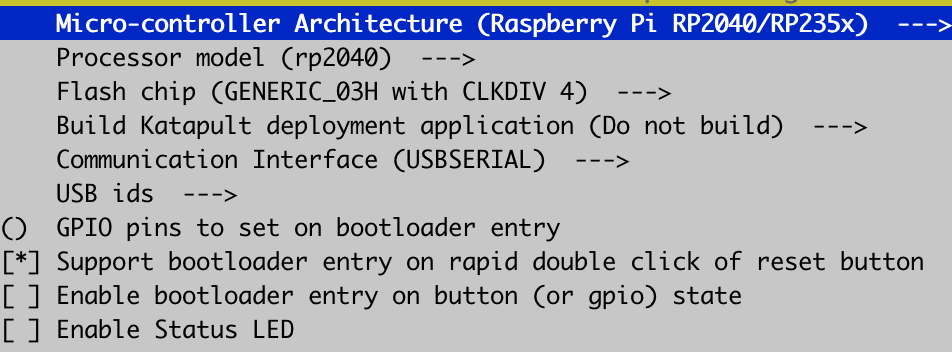
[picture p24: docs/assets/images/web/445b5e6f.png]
    

    Then, run:

    ```
    make clean
    make
    cp out/katapult.uf2 ~/printer_data/config/katapult.uf2
    ```

    Now in Mainsail/Fluidd, download `katapult.uf2` from your printer's config folder onto your computer and proceed to flashing.

=== "2. Download precompiled Katapult (compiled August 4, 2025)"
    Download [katapult.uf2](../assets/klipper/katapult.uf2) to your computer and proceed to flashing.

### Flashing Katapult

Now that you have `katapult.uf2` on your computer, install the BOOT and VUSB jumpers onto the SKR Pico as shown in the below diagram.



/// caption
Credits: Voron Design
///

Plug the SKR Pico into your computer with the USB-C cable that came with it. It should show up as a USB drive.

Drag `katapult.uf2` into the drive. It should quickly disconnect then reconnect itself.

Now, remove the BOOT jumper and unplug the Pico from your computer.

### Compiling Klipper

Now, SSH into your Pi again and run the following commands:

```
cd ~/klipper
make menuconfig
```

Adjust your `menuconfig` settings to match this exactly:

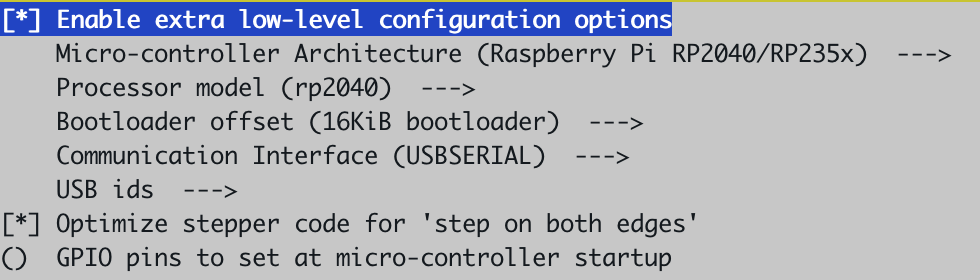
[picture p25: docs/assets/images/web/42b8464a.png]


Now, run:

```
make clean
make
```

### Flashing Klipper

Run in SSH:

```
ls /dev/serial/by-id/*
```

Plug the Pico into your Pi and double-click the RESET button.

```
ls /dev/serial/by-id/*
```

There should be a new USB device shown after plugging the Pico in. Copy the entire path, including `/dev/serial/by-id/`, and run the final commands:

```
cd ~/klipper
make flash FLASH_DEVICE=<PASTE HERE>
```

Your SKR Pico is now successfully flashed with Katapult and Klipper.

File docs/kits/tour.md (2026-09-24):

---
icon: material/map-search
comments: true
---

# 3MS Kits

## What's inside

<div class="grid cards" markdown>

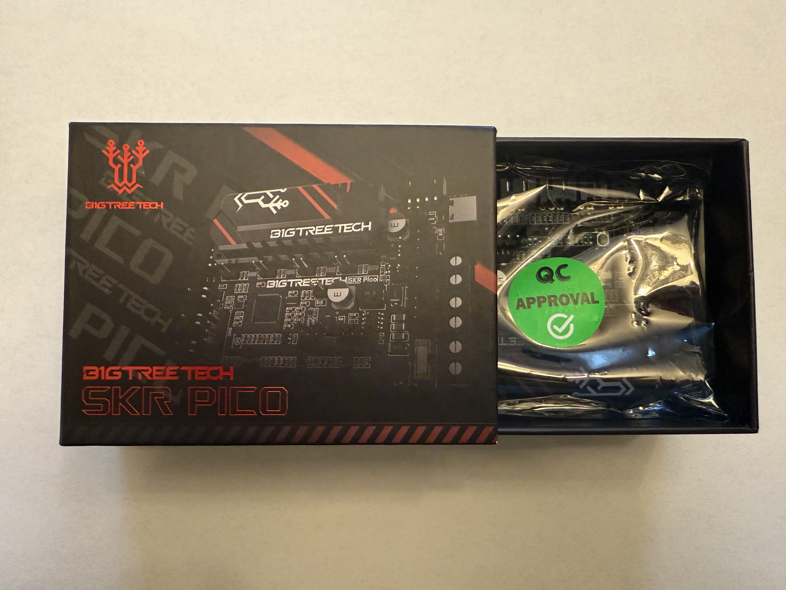
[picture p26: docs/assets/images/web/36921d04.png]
- 

    ---

    __BTT SKR Pico board__

    Each board is pre-flashed with the latest Klipper firmware and checked for MCU functionality.

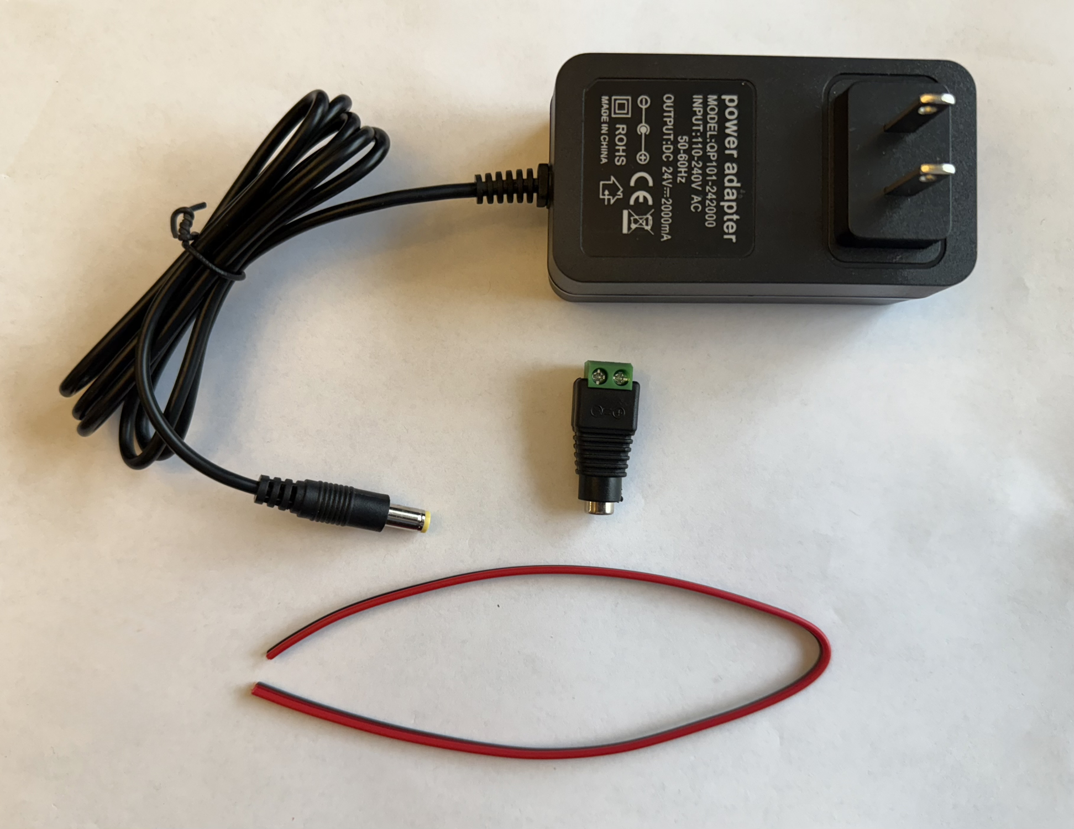
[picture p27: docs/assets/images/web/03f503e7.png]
- 

    ---

    __Power Supply__

    Each kit includes a PSU rated for 24V@2A, ~10in of black and red power cables, and an adapter to a screw terminal.

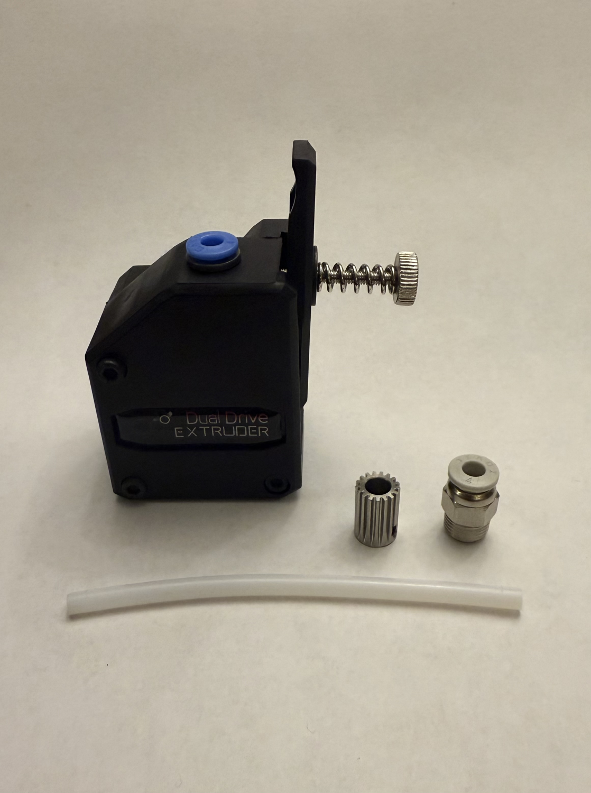
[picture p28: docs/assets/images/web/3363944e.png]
- 

    ---

    __Extruders__

    Each kit includes four BMG-style extruders to drive the filament.

- 

    ---

    __Stepper Motors__

    Each kit includes four NEMA17 stepper motors to drive the extruders.

- 

    ---

    __PTFE Tubing__

    Each kit includes 10ft of 2mmIDx4mmOD PTFE tubing, five PC4-M10 fittings, and five ECAS04 fittings so you can use any Y-splitter.

- 

    ---

    __3HOME Fasteners Kit__

    Each kit includes the necessary fasteners to build a 3HOME, the official modular enclosure for the 3MS.

</div>

## Includes

- 1x BTT SKR Pico board
- 1x PSU
- 1x PSU to screw terminal adapter
- 1x Power cables (black and red)
- 4x NEMA17 stepper motor
- 4x BMG-style extruder
- 1x PTFE tubing (10ft)
- 5x PC4-M10 bowden fittings
- 5x ECAS04 bowden fittings
- 1x 3HOME fasteners kit

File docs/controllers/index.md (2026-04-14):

---
comments: true
icon: fontawesome/solid/microchip
---

# Controllers

Follow this guide to determine which controller to use in your 3MS.

## Options

The 3MS works on multiple different controllers. 

!!! info
    If your printer's mainboard has spare stepper ports, you can use them to control 3MS steppers. You can open an issue on Github (there's a template) to get a configuration made for your specific setup. Any controllers listed with "(main MCU)" use those spare stepper plugs.

Choose one of the following supported controllers (a checked box indicates it is fully tested, and an empty box indicates testers wanted):

- [X] [SKR Pico (4 colors)](skrpico.md)

    !!! success "Recommended"
    
---

- [X] [BTT MMB V1 (4 colors)](bttmmb.md)
- [X] [SKR Mini E3 V2.0 (4 colors)](skrminie3v2.md)
- [X] [Einsy RAMBo (main MCU) with SKR Mini E3 V2.0 (3ms MCU)](einsyrambo-skrminie3v2.md)

    !!! warning "Expert modification"
    
- [X] [Geetech A30T](geetech-a30t.md)
- [ ] [Mellow Fly D7 (6 colors)](mellowflyd7.md)
- [ ] [Zonestar ZM384 (main MCU) (4 colors)](zm384main.md)
- [ ] [Mini RAMBo (4 colors)](minirambo.md)
- [ ] [BTT Octopus (main MCU) (4 colors)](bttoctopusmain.md)

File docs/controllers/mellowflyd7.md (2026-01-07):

---
comments: true
---

# Mellow Fly D7

**Max filament units: 7**

**MCU Name: `3ms`**

## BOM

| Name | Price | Quantity | Link | Notes |
| - | - | - | - | - |
| Mellow Fly D7 |  | 1 | | |
22AWG Cables | $9.99 | 1 | [Amazon](https://a.co/d/0oP9cD3) | These wires are only sufficient to run steppers, not heaters |
| 12V PSU | $7.39 | 1 | [Amazon](https://a.co/d/gLC1eli) | This PSU is only sufficient to run steppers, not heaters |

{{ filUnitBOM }}

## Wiring

Route the wires from the NEMA17's to the controller board. Follow this table to determine which port to plug the motors into:

| Filament Unit # | Motor Port |
| - | - |
| 0 | X |
| 1 | Y |
| 2 | Z |
| 3 | Z1 |
| 4 | Z2 |
| 5 | E0 |

Now, grab your 12V PSU and two M-M duponts, one red and one black (M-M means that there is metal coming out of both ends of the cable). Plug the PSU into the wall, but don't plug the screw terminals into the PSU (the screw terminals have green)

1. Plug the red wire into the positive terminal of the screw terminals
2. Plug the black wire into the negative terminal of the screw terminals

    !!! danger
        These dupont cables are too thin to run much more than the stepper motors. If you run a heater or other power-intensive device off of the board board, the duponts and/or PSU can melt/catch fire. To reduce the risk of this, you can double up on the duponts or get thicker wires.

5. Using the markings on the board, plug the red wire into the positive terminal on the board
6. Using the markings on the board, plug the black wire into the negative terminal on the board
7. Verify all connections

    !!! warning
        If the wires are plugged into the wrong place, or swapped polarities, your board, Stepper motors, and/or PSU can be badly damaged.

8. Plug the PSU screw terminals into the PSU wire

If the board lights up, you wired it correctly!

Finally, plug the board into your Klipper host with the cable that came with it.

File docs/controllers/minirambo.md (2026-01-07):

---
comments: true
---

# Mini RAMBo

**Max filament units: 4**

**MCU Name: `3ms`**

## BOM

| Name | Price | Quantity | Link | Notes |
| - | - | - | - | - |
| Mini RAMBo | | 1 | | |
22AWG Cables | $9.99 | 1 | [Amazon](https://a.co/d/0oP9cD3) | These wires are only sufficient to run steppers, not heaters |
| 12V PSU | $7.39 | 1 | [Amazon](https://a.co/d/gLC1eli) | This PSU is only sufficient to run steppers, not heaters |

{{ filUnitBOM }}

## Wiring

Route the wires from the NEMA17's to the controller board. Follow this table to determine which port to plug the motors into:

| Filament Unit # | Motor Port |
| - | - |
| 0 | XM |
| 1 | YM |
| 2 | ZAM or ZBM |
| 3 | E0M |

Now, grab your 12V PSU and two M-M duponts, one red and one black (M-M means that there is metal coming out of both ends of the cable). Plug the PSU into the wall, but don't plug the screw terminals into the PSU (the screw terminals have green)

1. Plug the red wire into the positive terminal of the screw terminals
2. Plug the black wire into the negative terminal of the screw terminals

    !!! danger
        These dupont cables are too thin to run much more than the stepper motors. If you run a heater or other power-intensive device off of the RAMBo board, the duponts and/or PSU can melt/catch fire. To reduce the risk of this, you can double up on the duponts or get thicker wires.

4. Route the two wires inside closest to your chosen input
5. Using the markings on the board, plug the red wire into the positive terminal on the RAMBo
6. Using the markings on the board, plug the black wire into the negative terminal on the RAMBo
7. Verify all connections

    !!! warning
        If the wires are plugged into the wrong place, or swapped polarities, your RAMBo, Stepper motors, and/or PSU can be badly damaged.

8. Plug the PSU screw terminals into the PSU wire

If the RAMBo lights up, you wired it correctly!

Finally, plug the RAMBo into your Klipper host with the cable that came with it.

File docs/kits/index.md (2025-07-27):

---
icon: material/package-variant-closed
status: new
---

# 3MS Kits

<style>
    .kits-buy-btn {
        width: 30%;
    }
</style>

(https://west3d.com/products/3ms-the-simple-and-reliable-multi-material-system-kit-by-3dcoded)

!!! info "Disclaimer"
    By using the 3MS, you agree to the terms outlined in the full disclaimer and accept full responsibility for its assembly and use. The creators are not liable for any damage, loss, or harm caused by the product.

    ??? "Full Disclaimer"
        ### Full Disclaimer

        The 3MS (Modular MultiMaterial System) is provided as-is, with no guarantees or warranties, expressed or implied, regarding its performance, safety, reliability, or suitability for any particular purpose. By purchasing, assembling, or using the 3MS, you acknowledge and agree to the following terms and conditions:

        1. **Assumption of Risk**
        The use, assembly, and operation of the 3MS are entirely at your own risk. You are solely responsible for ensuring the proper assembly, configuration, and operation of the product. The creators, contributors, and distributors of the 3MS are not liable for any damage, including but not limited to:

            - Damage to your 3D printer, components, or other equipment.
            - Property damage resulting from use or misuse.
            - Personal injury, including but not limited to burns, cuts, or other physical harm.

        2. **No Warranties or Guarantees**
        The 3MS is sold as a consumer-ready product designed for hobbyist use but is not guaranteed to function without issue in all environments or scenarios. While the instructions provided aim to ensure a successful assembly and operation, they may not account for every possible issue, user error, or unique configuration. No warranties, express or implied, including but not limited to fitness for a particular purpose, are provided.

        3. **Responsibility for Assembly and Use**
        Assembly of the 3MS requires basic technical skills, including mechanical assembly and firmware configuration. It is your responsibility to carefully follow the instructions and ensure all components are installed and configured correctly. Failure to do so may result in malfunction, damage, or injury, for which the creators, contributors, and distributors are not responsible.

        4. **Compatibility and Modifications**
        The 3MS is designed to be compatible with a variety of 3D printers, but compatibility is not guaranteed in all cases. Modifications to the hardware, firmware, or system setup may lead to unintended consequences, and the creators and distributors are not responsible for any resulting issues.

        5. **Void of Warranty**
        Use of the 3MS may void the warranty of your 3D printer and other components. The creators, contributors, and distributors are not liable for any issues related to warranty claims or repairs resulting from the use of the 3MS.

        6. **Indemnification**
        By using the 3MS, you agree to indemnify and hold harmless the creators, contributors, and distributors from any claims, damages, or liabilities arising from your use of the product, including but not limited to damages to personal property, injury, or harm caused by incorrect assembly, configuration, or operation.

        7. **Limitation of Liability**
        Under no circumstances will the creators, contributors, or distributors be liable for any indirect, incidental, special, or consequential damages arising from the use or inability to use the 3MS, including but not limited to loss of profits, data, or business opportunities, even if advised of the possibility of such damages.

        By purchasing or using the 3MS, you agree to the terms outlined in this disclaimer and release the creators, contributors, and distributors from any claims or liabilities arising from its use. If you do not agree to these terms, do not proceed with assembly or use of the 3MS.

## Tour

For a detailed look at what's included in 3MS kits, check out this tour below:

[:material-map: 3MS Kits Tour](tour.md){.md-button}

## Instructions

To assemble and set up your 3MS kit, follow the instructions below.

[:octicons-list-ordered-24: Instructions](../instructions/index.md){.md-button}

## Survey

I'd really appreciate it if you could take a couple minutes and fill out this quick [survey](https://forms.gle/bcG71buCrVxnpp767) about your experience with the kit.

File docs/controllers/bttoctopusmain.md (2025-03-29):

---
comments: true
---

# BTT Octopus (main MCU)

!!! warning
    This configuration may not work with the BTT Octopus Pro.

**Max filament units: 4**

**MCU Name: `main`**

## main MCU

This configuration is a `main MCU` configuration, meaning that your printer should already be running off a BTT Octopus and you don't need to purchase one.

## BOM

Per filament unit:

[1x TMC2209](https://a.co/d/01KA3Y1) ($7 each)

{{ filUnitBOM }}

## Wiring

Route the wires from the NEMA17's to the controller board. Follow this table to determine which port to plug the motors into:

| Filament Unit # | Motor Port |
| - | - |
| 0 | MOTOR7 |
| 1 | MOTOR6 |
| 2 | MOTOR5 |
| 3 | MOTOR4 |

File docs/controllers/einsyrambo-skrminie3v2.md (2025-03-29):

---
comments: true
---

# Einsy RAMBo (main MCU) with SKR Mini E3 V2

!!! danger
    This guide is an expert guide only

!!! info
    This modification is designed for the Prusa MK3/S/S+, and depends on [this](https://github.com/dz0ny/klipper-prusa-mk3s) Klipper configuration.

## Why?

When printing fast, the TMC2130's on the Einsy RAMBo can get quite loud. The TMC2209's on the SKR Mini are much quieter and support denser microstepping.

## BOM

| Name | Price | Quantity | Link | Notes |
| - | - | - | - | - |
| PSU -> Einsy Cable | $7.99 | 1 | [PartsBuilt3D](https://www.partsbuilt.com/cable-psu-to-einsy-for-prusa-mk3-3s-3s-prusa-compatible/) | |
| Stepperonline NEMA17 | $9.99 each | [Amazon](https://a.co/d/el99D6X) | 2 | Replaces current XY motors |

{{ filUnitBOM }}

## Wiring

First, unplug the 3MS steppers from the SKR Mini, and the XY steppers from the Einsy RAMBo. The motors will need to be switched due to different connector types between boards.

This table outlines the major wiring of this modification.

| Einsy RAMBo | SKR Mini E3 V2 | Motor
| - | - | - |
| PSU+ | POWER+ | |
| PSU- | POWER- | |
| XM | | 3ms0 |
| YM | | 3ms1 |
| | XM | X |
| | YM | Y | 

## Configuration

In your `printer.cfg`, comment out these lines:

```cfg title="printer.cfg"
#[include klipper-prusa-mk3s/mk3s/steppers.cfg]
#[include klipper-prusa-mk3s/mk3s/tmc2130.cfg]
```

Next, copy the contents of `3ms/controllers/einsy_rambo_with_skr_mini/xy-motors.cfg` and `ze-motors.cfg` to `klipper-prusa-mk3s/skr/xy.cfg`, and `klipper-prusa-mk3s/mk3s/ze.cfg`, respectively.

Add the following new lines:

```cfg title="printer.cfg"
[include klipper-prusa-mk3s/skr/xy.cfg]
[include klipper-prusa-mk3s/mk3s/ze.cfg]
```

Restart Klipper.

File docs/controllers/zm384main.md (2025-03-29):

---
comments: true
---

# Zonestar ZM384 (main MCU)

**Max filament units: 3**

**MCU Name: `main`**

## main MCU

This configuration is a `main MCU` configuration, meaning that your printer should already be running off a ZM384 and you don't need to purchase one.

{{ filUnitBOM }}

| Filament Unit # | Motor Port |
| - | - |
| 0 | E0 |
| 1 | E1 |
| 2 | E2 |
| 3 | E3 |

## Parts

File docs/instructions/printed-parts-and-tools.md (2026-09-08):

---
icon: material/tools
comments: true
---

<link rel="stylesheet" href="../../../assets/css/kits.css">

# Printed Parts & Tools

###**Step 1** 3HOME Enclosure

<div class="grid cards" markdown>
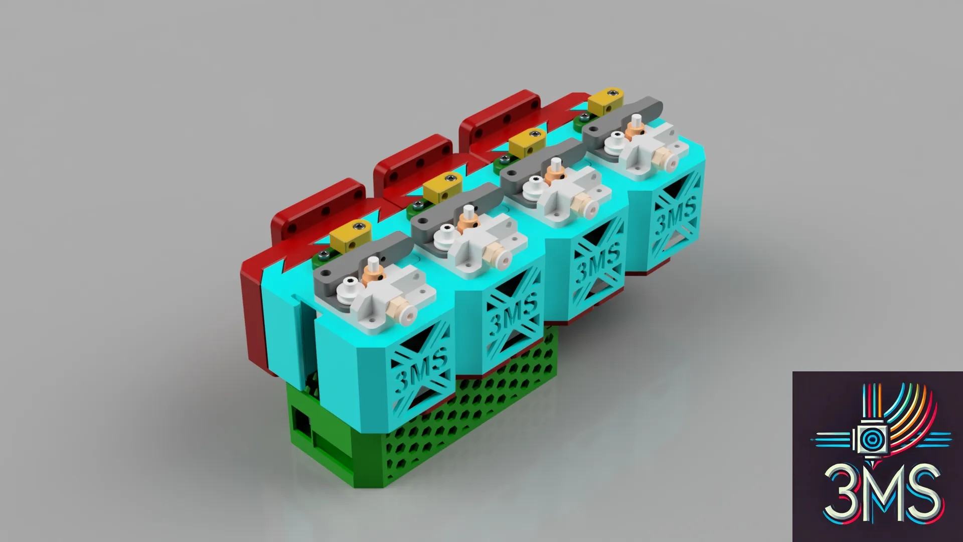
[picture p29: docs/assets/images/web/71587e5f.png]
- 

- Print out the 3HOME Official Modular Enclosure for the 3MS.

    [:material-printer: Printables](https://www.printables.com/model/1108644-beta-3home-3ms-hybrid-official-modular-enclosure/files){.md-button}

</div>


###**Step 2** Y-splitter

<div class="grid cards" markdown>
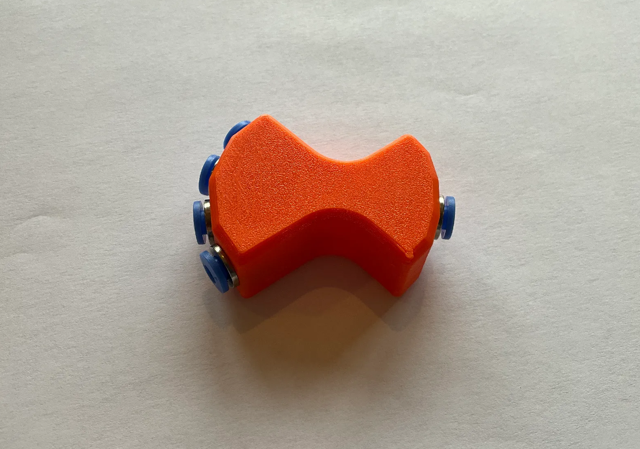
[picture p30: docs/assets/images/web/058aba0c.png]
- 

- Print out one 4-way Y-splitter.

    !!! note "Alternate Splitters"
        The linked Y-splitter uses five ECAS04 fittings, which are included in your 3MS kit. For your convenience, five PC4-M10 fittings are also included if you prefer to use an alternate Y-splitter design.

</div>


###**Step 3** Hex Keys

<div class="grid cards" markdown>
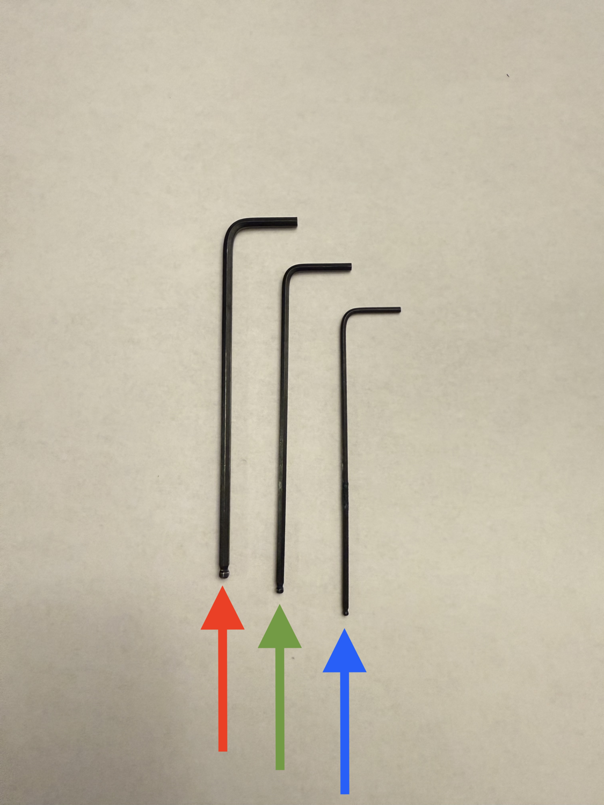
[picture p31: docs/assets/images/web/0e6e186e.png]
- 

- Ensure you have the following hex keys:

    :red_circle: 1.5mm (included in kit but recommended to get your own)

    :green_circle: 2mm

    :blue_circle: 2.5mm (included in the kit but recommended to get your own)

</div>


###**Step 4** Phillips & Flat-head Screwdrivers

<div class="grid cards" markdown>
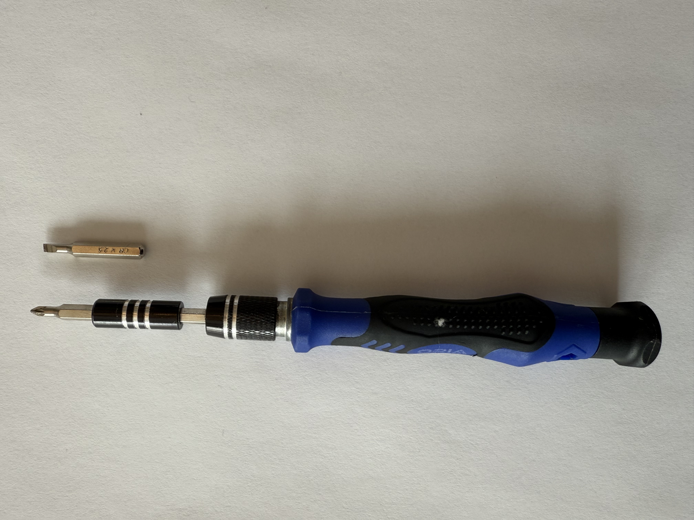
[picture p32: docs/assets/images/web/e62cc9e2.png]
- 

- Ensure you have:

    - A phillips-head screwdriver (used for the screw terminals for the PSU)

    - A flat-head screwdriver (used for the screw terminals on the SKR Pico)

</div>


###**Step 5** Wire Strippers

<div class="grid cards" markdown>
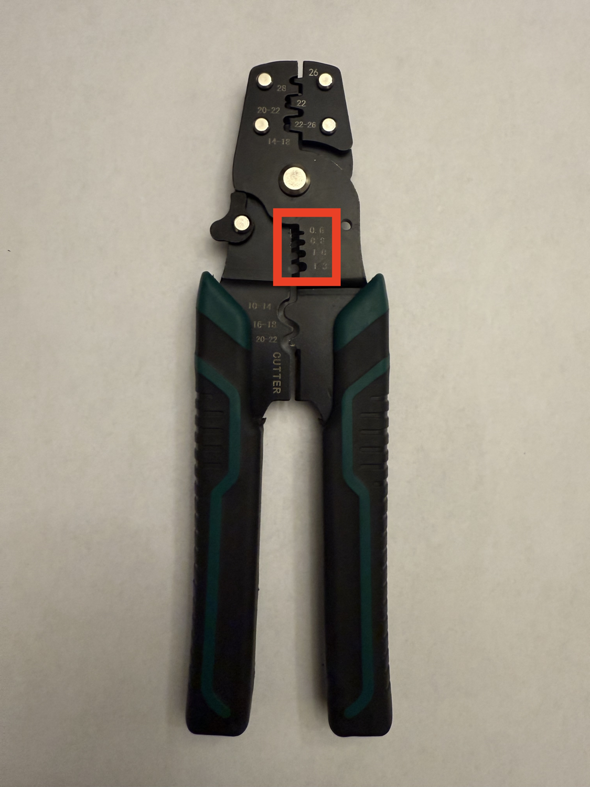
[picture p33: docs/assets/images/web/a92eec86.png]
- 

- :red_circle: Ensure you have wire strippers capable of stripping 24AWG wire (0.25mm^2^)

</div>


###**Step 6** Side Cutters

<div class="grid cards" markdown>
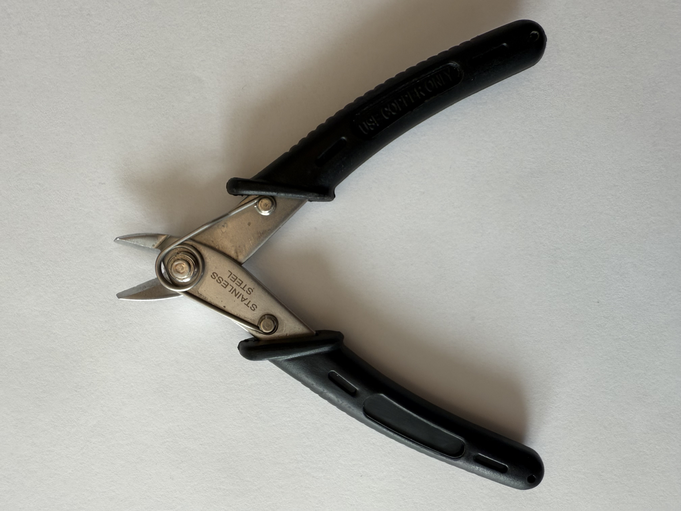
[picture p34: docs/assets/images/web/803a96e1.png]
- 

- Ensure you have side cutters (used for cutting zip ties)

</div>


###**Step 7** PTFE Cutters

<div class="grid cards" markdown>
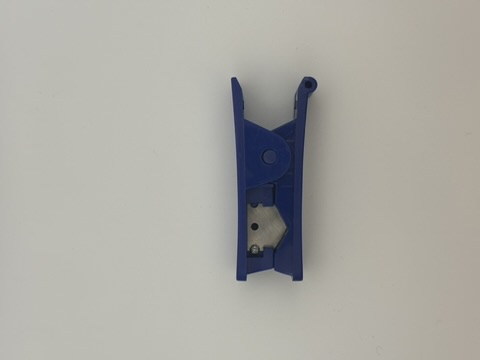
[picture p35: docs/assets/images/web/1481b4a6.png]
- 

- Ensure you have a PTFE cutting tool. Alternatively, you can [print](https://www.printables.com/model/360710) a tool to cut the PTFE.

</div>


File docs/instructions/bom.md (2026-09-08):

---
icon: material/cart
comments: true
---

# BOM

## Controller Choice

First, choose the control board you want to use in your 3MS. Choose a controller from the available ones [here](../controllers/index.md).

## Number of filament units

First, choose the number of filament units you want. Each filament unit lets you print with an additional filament. Two filament units are the minimum. You can add or remove filament units after building, but the BOM and configuration will vary based on how many filament units you want.

## Controller BOMs

Choose the BOM for your chosen controller from the list below:

**Recommended: [BTT SKR Pico](../controllers/skrpico.md)**

??? "Other Controllers"

    [BTT SKR Mini E3 V2](../controllers/skrminie3v2.md#bom)

    [BTT MMB](../controllers/bttmmb.md#bom)

    [Mellow Fly D7](../controllers/mellowflyd7.md#bom)

    [BTT Octopus (main MCU)](../controllers/bttoctopusmain.md#bom)

    [Zonestar ZM384 (main MCU)](../controllers/zm384main.md)

    [Mini RAMBo](../controllers/minirambo.md#bom)

    [Geetech A30T](../controllers/geetech-a30t.md#bom)

## Filament Unit BOMs

For each filament unit, purchase the following:

| Name | Quantity | Price | Link | Notes |
| - | - | - | - | - |
| NEMA17 Stepper Motor | 1 | $9.99 | [Amazon](https://a.co/d/06Lsa1qI) | You can use a pancake stepper if you want, but it will have less torque
| BMG Clone Extruder | 1 | $9.99 | [Amazon](https://a.co/d/fp2GNRQ) | Alternatively, you can use [this](https://a.co/d/dbw7Wor) Dual-drive MK8 based extruder |
| PTFE Tubing | 1 | $8.99 | [Amazon](https://a.co/d/7FAhmS5) | You likely won't need this for every unit, as this is usually too long for only one unit |

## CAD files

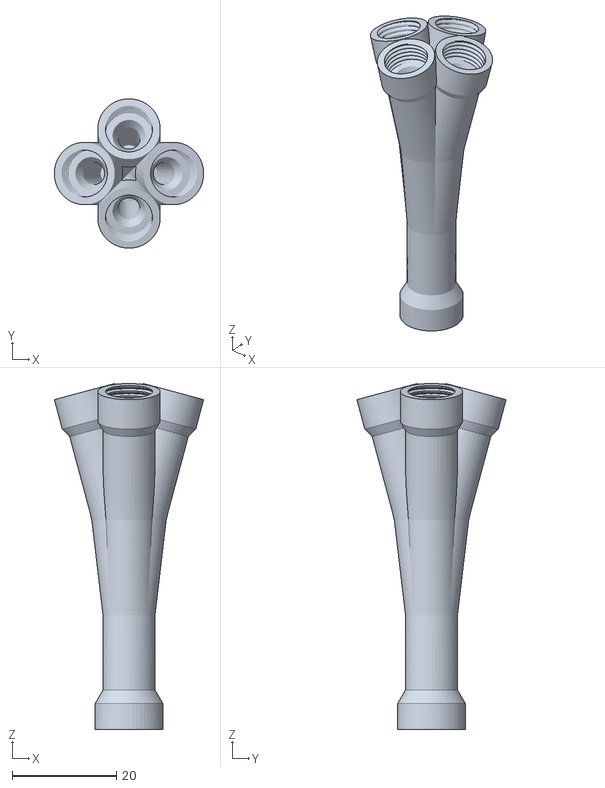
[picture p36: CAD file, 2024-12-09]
docs/assets/stls/4ysplitter.stl
28.6 x 28.6 x 66.4

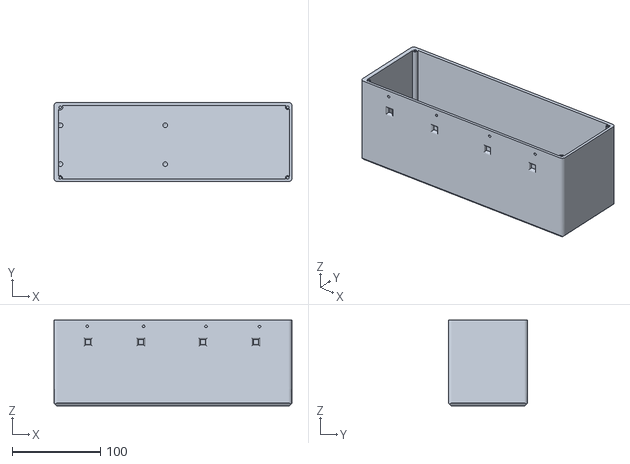
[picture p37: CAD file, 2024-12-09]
docs/assets/stls/enclosure/bottom-v6.stl
270.0 x 90.0 x 97.0

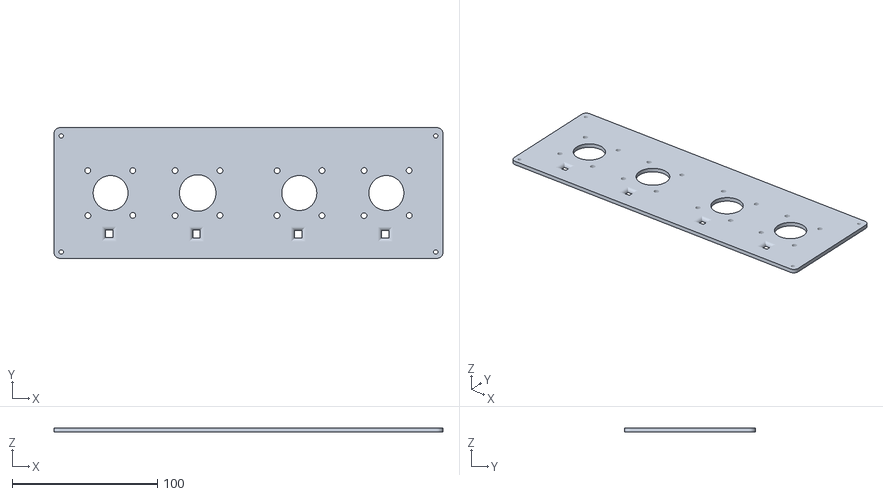
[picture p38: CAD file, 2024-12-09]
docs/assets/stls/enclosure/top-v6.stl
268.0 x 90.0 x 3.00

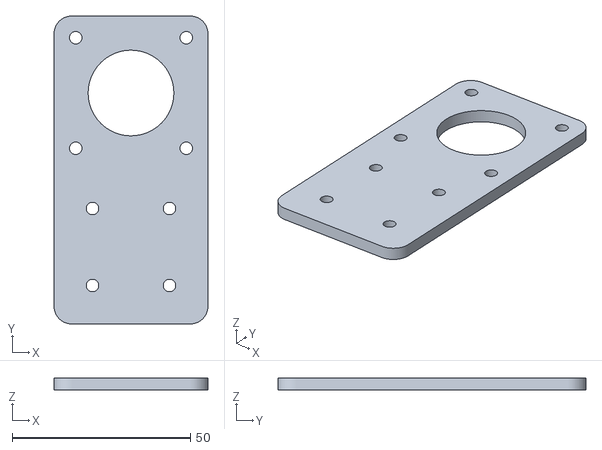
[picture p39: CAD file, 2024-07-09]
docs/assets/stls/mk8m3.stl
43.2 x 86.4 x 3.50

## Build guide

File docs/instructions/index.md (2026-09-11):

---
icon: octicons/list-ordered-24
description: Instructions for building and setting up the 3MS modular multimaterial system for Klipper 3D printers.
comments: true
---

<link rel="stylesheet" href="../assets/css/badges.css">

<style>
.inst-button {
    width: 35ch;
    text-align: center;
}
</style>

# Master Instructions

Follow this guide to assemble your 3MS. A special thank you if you purchased a kit!

Feel free to ask on the 3DCoded Discord any time if you need help during your build!

Discord Shield (https://discord.gg/ekqxDhdGCg)

## Chapters

[**:material-cart: Getting a BOM**](bom.md){.inst-button .md-button}

[**:material-tools: Printed Parts and Tools**](printed-parts-and-tools.md){.inst-button .md-button}

[**:octicons-gear-24: Hardware Assembly**](hardware-assembly.md){.inst-button .md-button}

[**:fontawesome-solid-microchip: Electronic Assembly**](electronic-assembly.md){.inst-button .md-button}

[**:material-puzzle: Final Assembly**](final-assembly.md){.inst-button .md-button}

[**:material-console: Software Setup**](software-setup.md){.inst-button .md-button}

[**:material-code-json: Configuration**](config.md){.inst-button .md-button}

[**:fontawesome-solid-ruler: Calibration**](calibration.md){.inst-button .md-button}

[**:fontawesome-solid-flag-checkered: Slicer Setup and First Print**](firstprint.md){.inst-button .md-button}

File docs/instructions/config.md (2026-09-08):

---
comments: true
icon: material/code-json
---

# Configuration

After installing Happy Hare firmware, there are some configurations you need to go through before printing in multimaterial.

## Kit Users (SKR Pico)

If you built your 3MS from a kit or are using the SKR Pico board, set a starting rotation distance as shown:

<video src="/assets/videos/gearratio.mp4" controls></video>

Set `Other Settings` → `Gear Stepper` → `Gear Ratio` → `50:17`

## Filament Sensors

!!! info "Required Sensors"
    To use the 3MS, you'll need a filament sensor somewhere between your Y-splitter and printer extruder.

    There are two options for this sensor:

    - [**Shared gate sensor**](#shared-gate-sensor) is closer to the Y-splitter
    - [**Extruder entry sensor**](#extrudertoolhead-sensors) is closer to the printer's extruder.

    Assuming you already have one installed, you can configure it in the installer.

### Extruder/Toolhead Sensors

To configure an extruder entry sensor (a sensor right **before** your extruder):

!!! tip "Don't know where to find a sensor?"
    If you don't know where to find a good sensor for your printer, here are a few tips:

    - Search [Printables](https://www.printables.com/) and [Thangs](https://thangs.com/) for a sensor.
    - Build a [Filatector](https://github.com/ArmoredTurtle/Filatector) universal filament sensor.

!!! tip "Don't know your sensor pin?"
    If you don't know your sensor pin, and it's already configured with Klipper, locate your sensor configuration (usually `filament_switch_sensor`) and note the `sensor_pin`.

The below video shows where to find the pin settings. Note that your pins will likely be different.

<video src="/assets/videos/extsensor.mp4" controls></video>

To configure your toolhead sensor (a sensor right **after** your extruder), set your `toolhead_switch_pin` the same way as you set your `extruder_switch_pin`.

---

!!! warning "Existing Sensors"
    Before moving on, ensure all your existing `filament_switch_sensor` and `filament_motion_sensor` sections are commented out or deleted. Leaving this enabled will lead to unintended issues later on.

---

## Distances

There are many key distances to set up in Happy Hare firmware.

### Parking Position

The parking position is the location your filament should park when idle, measured from your gate endstop. This should be set to ~1-2cm above your Y-splitter.

To determine this value, begin by moving the filament in gate 0 to the ideal parking position by hand.

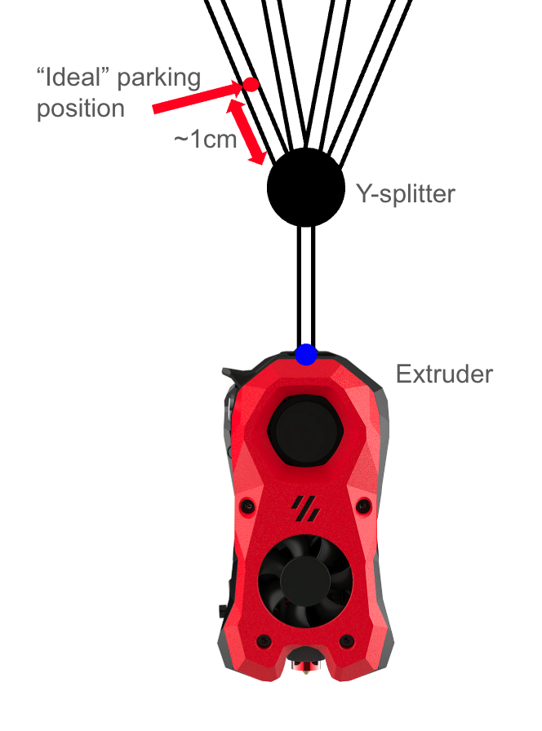
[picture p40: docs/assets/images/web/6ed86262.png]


Estimate the distance from your extruder to the ideal parking position. You can use a piece of filament outside of the tube and use a ruler to help measure this. In the diagram above, it's the distance between the red and blue dots. 

Save this value for configuration in the next step.

### Homing Distance

Firstly, configure the maximum distance Happy Hare should attempt to load filament to the homing sensor, before "giving up" and deciding that the spool is empty. This should usually be ~150% the distance from your filament parking position to the sensor.

<video src="/assets/videos/homingdistance.mp4" controls></video>

### Eject Distance

Finally, if you want to switch out which filament is in a filament unit, edit your final eject distance. This should be the distance from your parking position to your filament unit gears, plus a small margin.

<video src="/assets/videos/ejectdistance.mp4" controls></video>

## Speeds

There are a few main speeds you can configure with Happy Hare firmware.

- **Homing Speed**: This is when the HH moves the filament into your extruder entry sensor to ensure they are present.
- **Load/Unload Speed**: This is the speed at which Happy Hare will load/unload filament during a toolchange.
- **Extruder Speed**: This is the speed at which your extruder will load/unload filament during a toolchange.

<video src="/assets/videos/speeds.mp4" controls></video>

## Toolhead Distances

There are many key distances to setup in Happy Hare firmware, this time for the measurements of your toolhead.

There are three main ways to get any of the following distances:

- **Recommended:** Find and select your toolhead in the installer
- Find configs available online for your toolhead
- Use CAD models of your toolhead
- Measure (approximate) yourself with a piece of filament and calipers

All the below settings can be found in the `Toolhead Settings` section of the installer.

<video src="/assets/videos/toolheadsettings.mp4" controls></video>

### Homing Max

`toolhead_homing_max` is the maximum distance from the gate endstop to your extruder endstop HH will attempt to load filament.

!!! info "This parameter is only relevant if you use **both** an extruder entry sensor and a shared gate sensor"

### Manual Configuration

If you cannot find a pre-configured toolhead, you can manually configure the distances.

There are three main parameters to measure inside your toolhead.

- `toolhead_extruder_to_nozzle`

    This is the distance between your extruder gears and the nozzle. If you don't have access to CAD of your printer's toolhead, you can follow the below procedure to approximate it.

    1. Preheat your nozzle to printing temperatures.
    1. Press a piece of filament up against the entrance to your extruder gears.
    1. Using KlipperScreen/Mainsail/Fluidd controls, load the filament in until it barely starts oozing out of the nozzle. Note the total distance traveled. This is your approximate `toolhead_extruder_to_nozzle`

- `toolhead_sensor_to_nozzle`

    !!! info "This parameter is only relevant if you have a toolhead sensor."

    This is the distance between your toolhead sensor and nozzle. An easy way to approximate this is:

    1. Preheat your nozzle to printing temperatures.
    1. Press a piece of filament up against the entrance to your extruder gears.
    1. Using KlipperScreen/Mainsail/Fluidd controls, load the filament in until it triggers the toolhead sensor. Note the total distance traveled. Set `toolhead_sensor_to_nozzle` to `toolhead_extruder_to_nozzle - <MEASURED DISTANCE>`

- `toolhead_entry_to_extruder`

    !!! info "This parameter is only relevant if you have an extruder entry sensor."

    This is the distance between your extruder entry sensor and extruder gears. To approximate this:

    1. Take a scrap of filament and slowly push it into your toolhead until the extruder entry sensor triggers.
    1. Brace a marker against the top of your toolhead and mark the filament.
    1. Push filament further in until it hits the extruder gears.
    1. Put another mark on the filament.
    1. Remove the filament and measure the distance between the two marks. This is your `toolhead_entry_to_extruder` value.

## Optional Settings

Most users likely won't have to follow the below steps, as they are automatically set on most systems.

### Shared Gate Sensor

This is not required on most systems (most systems use an extruder entry sensor instead).

Moving backwards from the extruder, the next possible sensor you may have installed is a shared gate sensor. This goes right **after** the Y-splitter.

If you have a gate sensor installed, set your `gate_switch_pin`:

<video src="/assets/videos/sharedgate.mp4" controls></video>

### Pre-Gate or Post-Gear

This is not required on most systems.

Pre-gate sensors go **before** each of your filament units. Post-gear sensors go **after** each of your filament units.

<video src="/assets/videos/prepostgate.mp4" controls></video>

### Gate Homing Endstop

This is an optional step as on most systems this is automatically set.

When homing filament (checking if it is present), you have three options for the sensor to be used:

- **Shared Gate Sensor** Use the shared gate sensor after the Y-splitter
- **Post Gate Sensors** Use the individual post-gate sensors.
- **Extruder Sensor** Use the extruder entry sensor.

Select one of the three options. Note that only the available options will be enabled. In the below example only an extruder sensor is configured, so it is the only displayed option.

<video src="/assets/videos/gatehoming.mp4" controls></video>

### Extruder Homing Endstop

This is an optional step as on most systems this is automatically set.

Happy Hare also needs a reference sensor inside the toolhead. You have two main options for this:

- **Toolhead Sensor** Use the extruder entry sensor.
- **Compression Sensor** Use a sync-feedback sensor as a homing endstop.
- **None** Don't home inside the extruder.

Select one of the three options. Note that only available options will be shown depending on your setup.

<video src="/assets/videos/extruderhoming.mp4" controls></video>

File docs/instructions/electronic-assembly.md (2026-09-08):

---
title: Electronics Assembly
icon: fontawesome/solid/microchip
comments: true
---

<link rel="stylesheet" href="../../../assets/css/kits.css">

# Electronics Assembly

###**Step 1** Removing Supports: Part 1

<div class="grid cards" markdown>
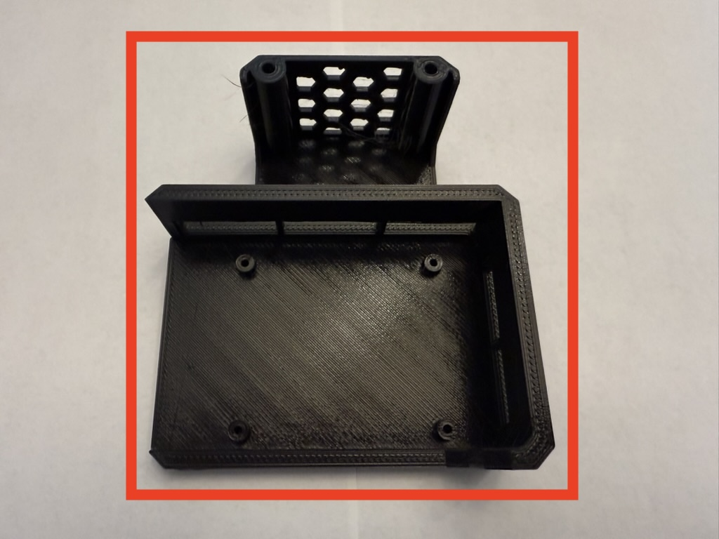
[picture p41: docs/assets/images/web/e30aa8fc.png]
- 
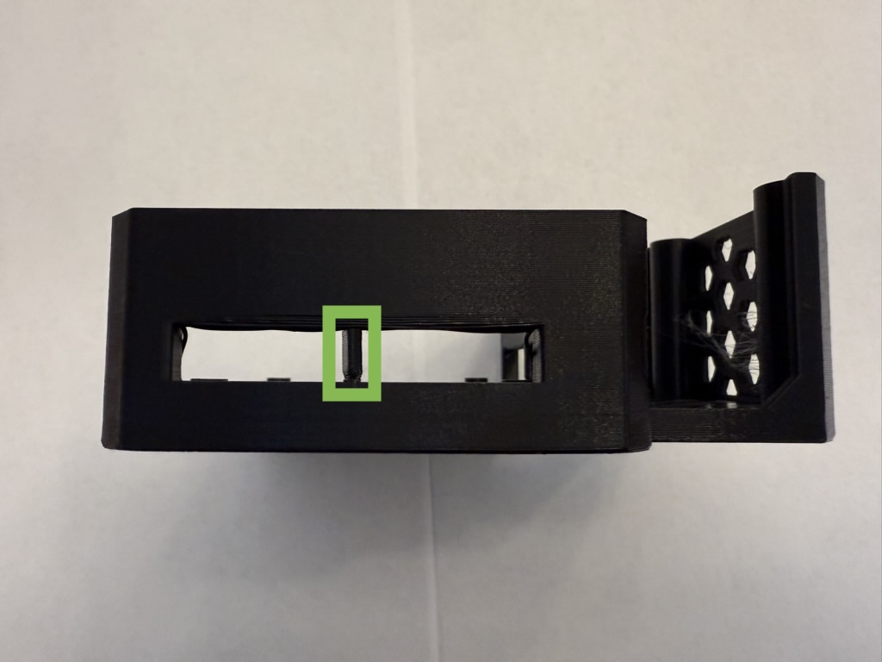
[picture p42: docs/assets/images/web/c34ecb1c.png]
    
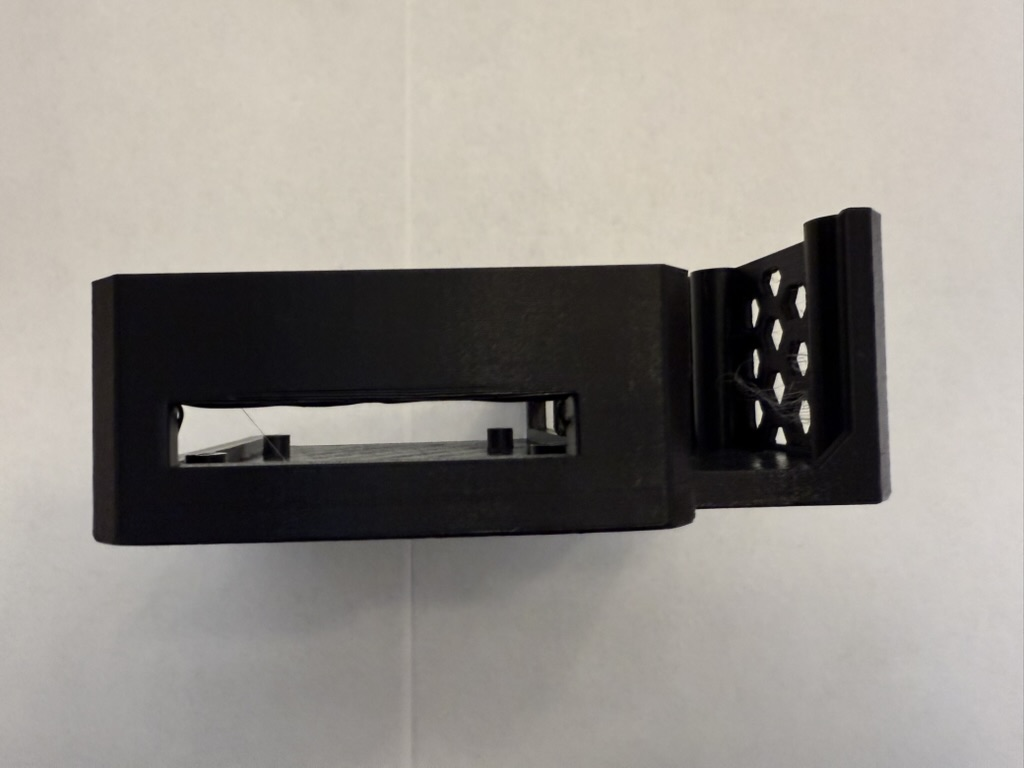
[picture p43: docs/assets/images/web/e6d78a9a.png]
    

- Remove the built-in supports from the SKR Pico case.

    :red_circle: Prepare either `SKR Pico Bottom.stl` or `SKR Pico Bottom (small).stl` (shown)

    :green_circle: Remove the indicated built-in support.

</div>




###**Step 2** Removing Supports: Part 2

<div class="grid cards" markdown>
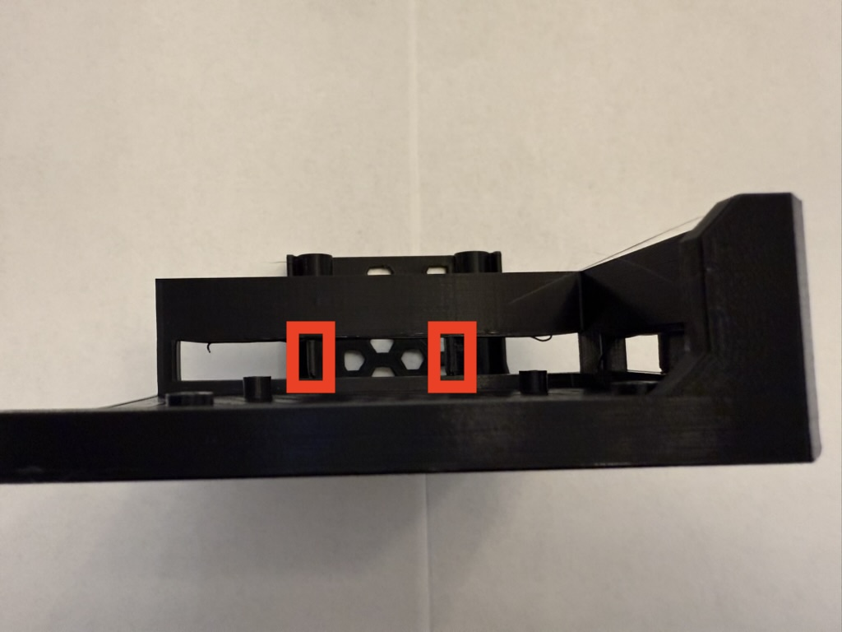
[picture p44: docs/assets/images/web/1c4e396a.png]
- 
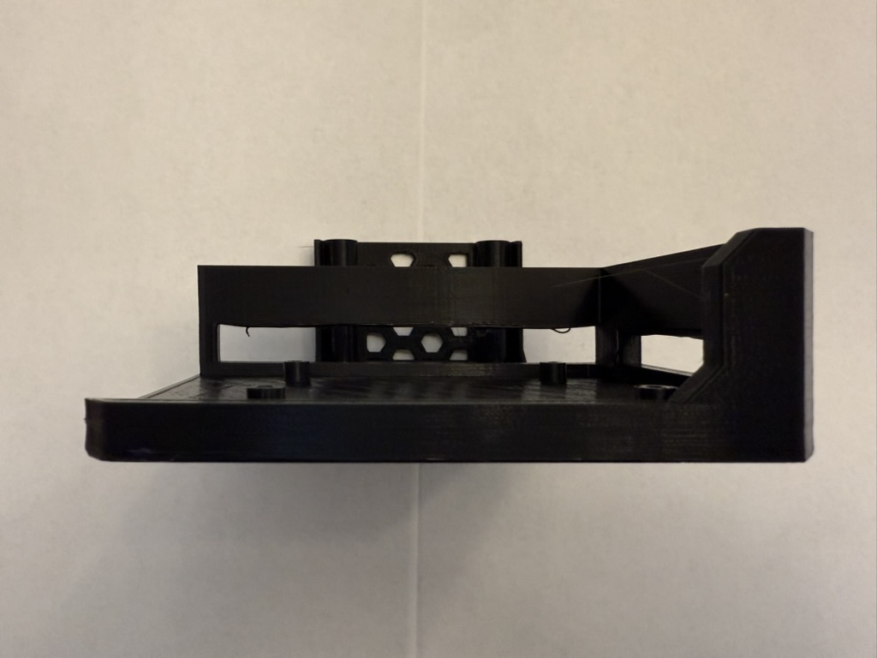
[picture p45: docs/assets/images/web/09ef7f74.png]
    

- Remove the built-in supports from the case.

    :red_circle: Remove the indicated supports from the case.

</div>



###**Step 3** Installing the Board

<div class="grid cards" markdown>
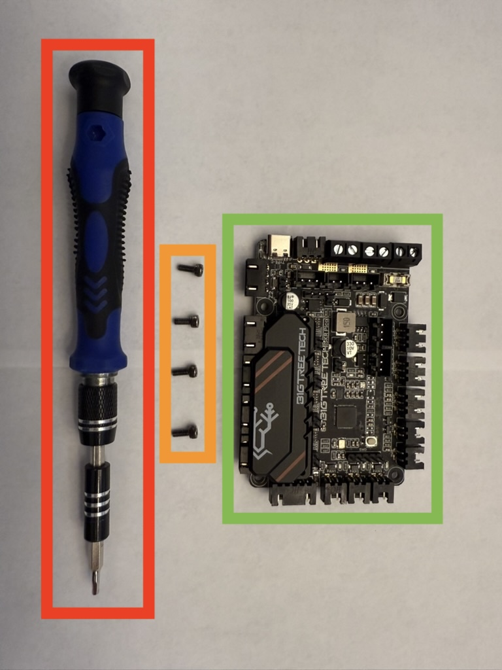
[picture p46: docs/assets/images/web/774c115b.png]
- 
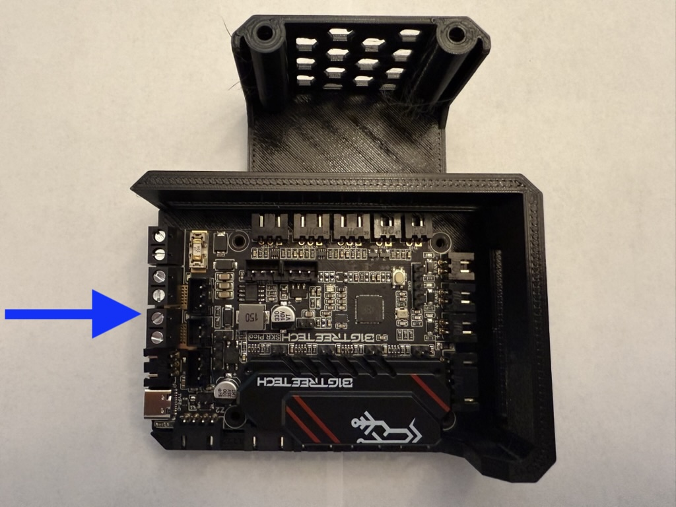
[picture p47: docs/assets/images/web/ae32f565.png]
    
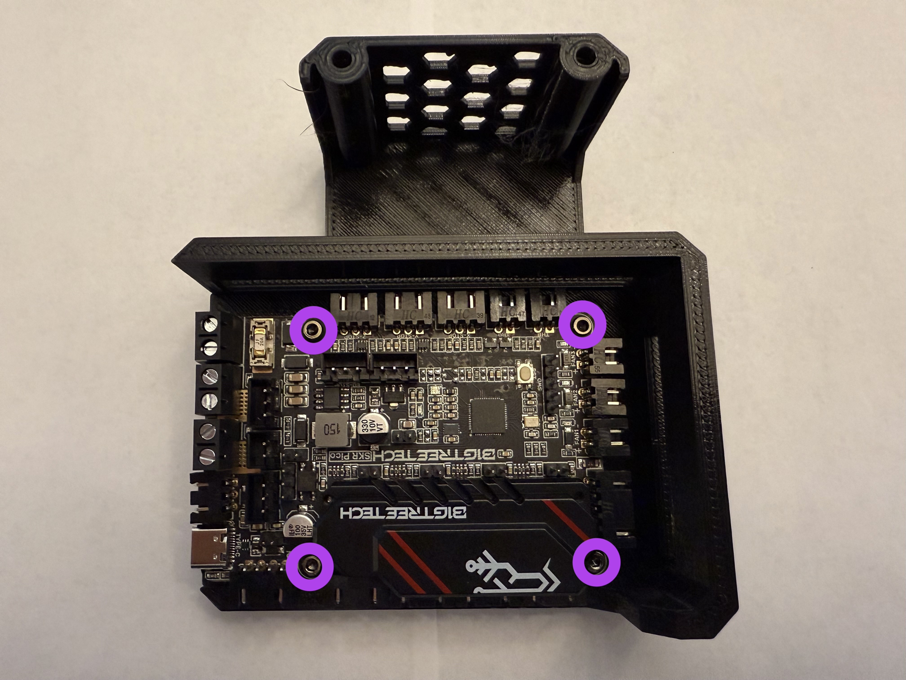
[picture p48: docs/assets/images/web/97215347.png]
    

- Install the SKR Pico board into the case.

    Prepare the following for this step:

    :red_circle: 2mm Hex key

    :orange_circle: 4x mounting bolts (included with the SKR Pico)

    :green_circle: SKR Pico board

    :blue_circle: Place the SKR Pico board onto the previously prepared case.

    :purple_circle: Using the four mounting bolts and the hex key, fasten the SKR Pico onto the case.

</div>




###**Step 4** Preparing the Power Cables

<div class="grid cards" markdown>
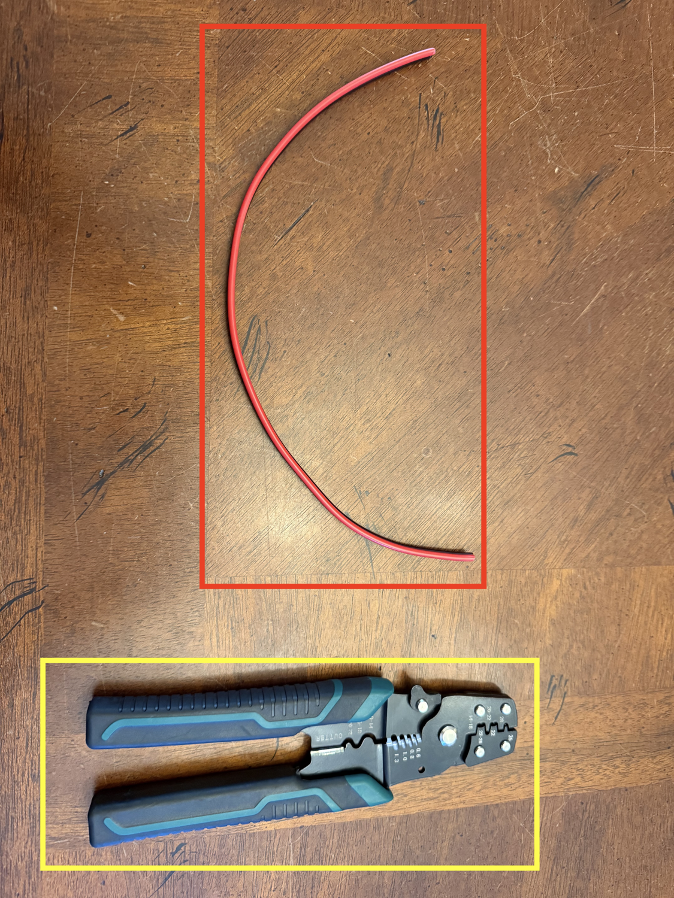
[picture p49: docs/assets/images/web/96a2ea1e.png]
- 
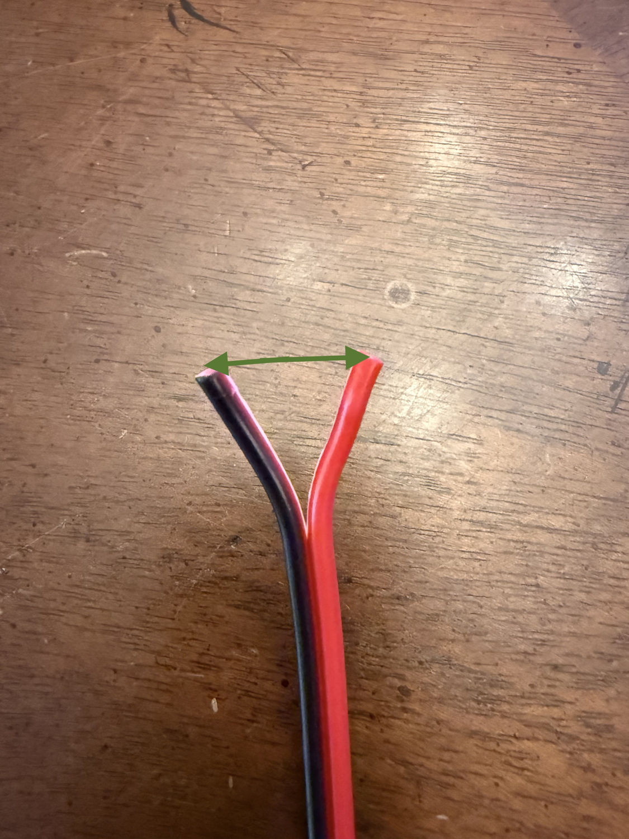
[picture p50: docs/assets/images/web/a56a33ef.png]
    
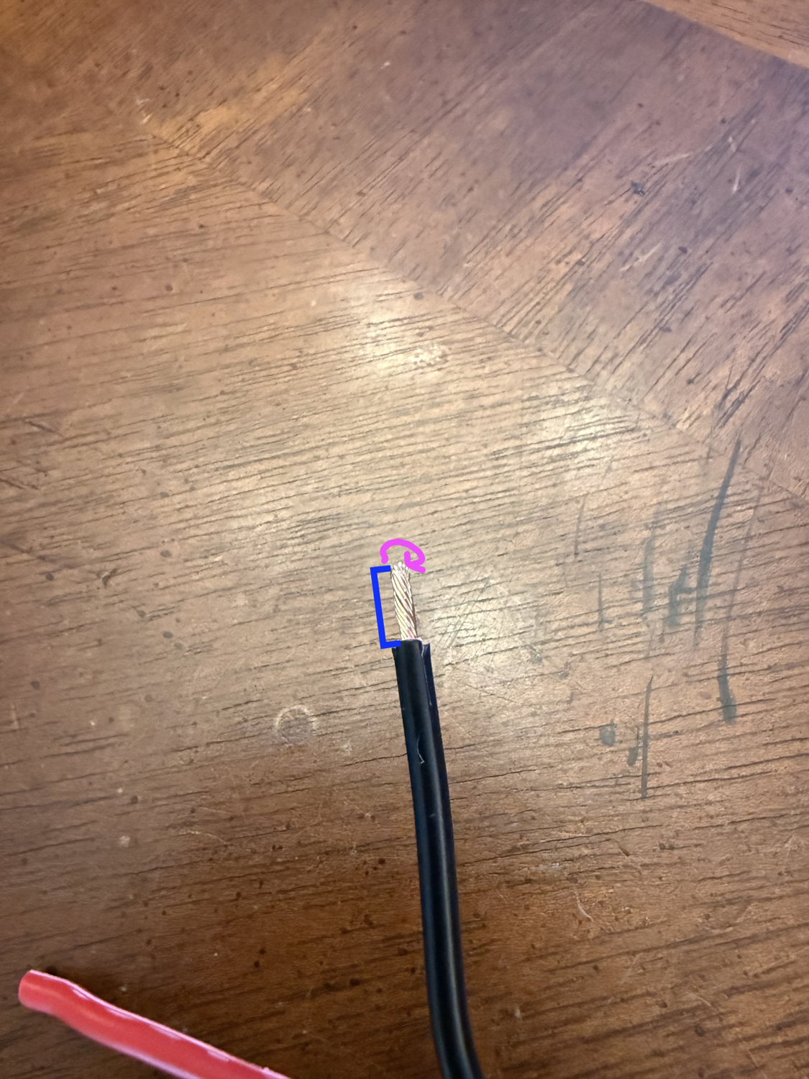
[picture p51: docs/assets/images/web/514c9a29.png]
    
    

- Strip the power cables and prepare for the next steps.

    Prepare the following for this step:

    :red_circle: Power cables

    :orange_circle: Wire strippers

    :green_circle: Split both ends of the wires as shown.

    :blue_circle: Strip a short length off of all four ends of the wires.

    :purple_circle: Twist the ends of the wires.

</div>





###**Step 5** Connecting the PSU

Connect the power cables to the PSU

  Prepare the following for this step:

  - Power cables
  - PSU
  - Phillips-head screwdriver

  To connect:

  1. Loosen both power terminals on the PSU.
  2. Plug the **red** wire into the **positive** terminal on the PSU.
  3. Plug the **black** wire into the **negative** terminal on the PSU.
  4. Tighten both power terminals on the PSU.

###**Step 6** Connecting the Power Cables

<div class="grid cards" markdown>
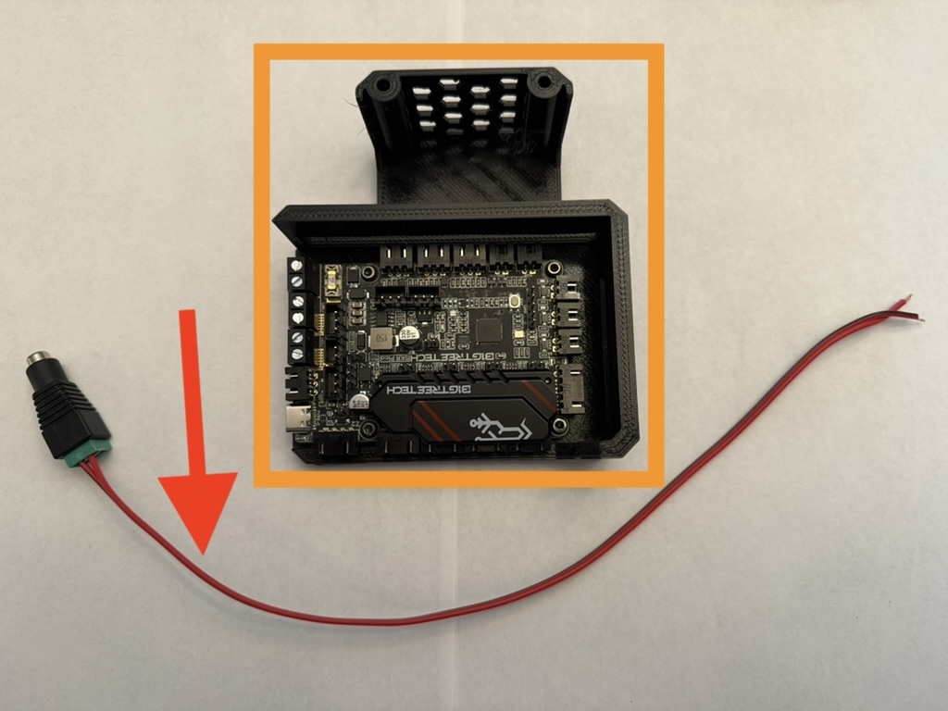
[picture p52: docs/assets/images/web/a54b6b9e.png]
- 
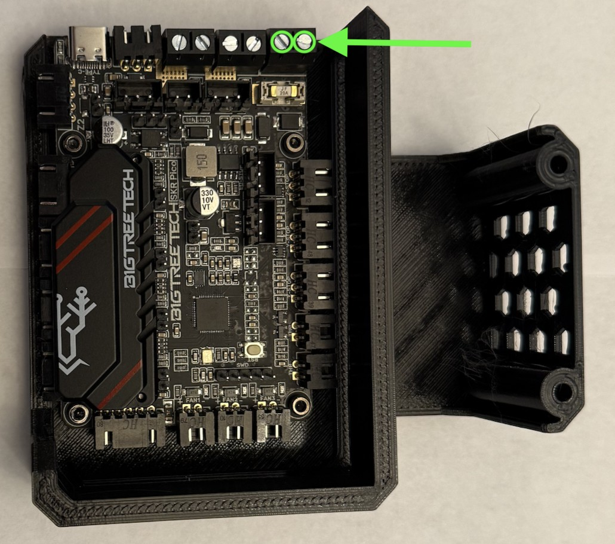
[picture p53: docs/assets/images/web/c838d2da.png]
    
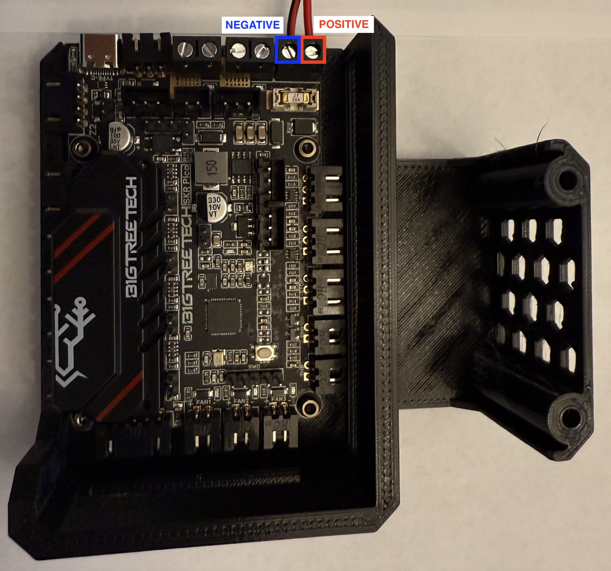
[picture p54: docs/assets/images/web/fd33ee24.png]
    
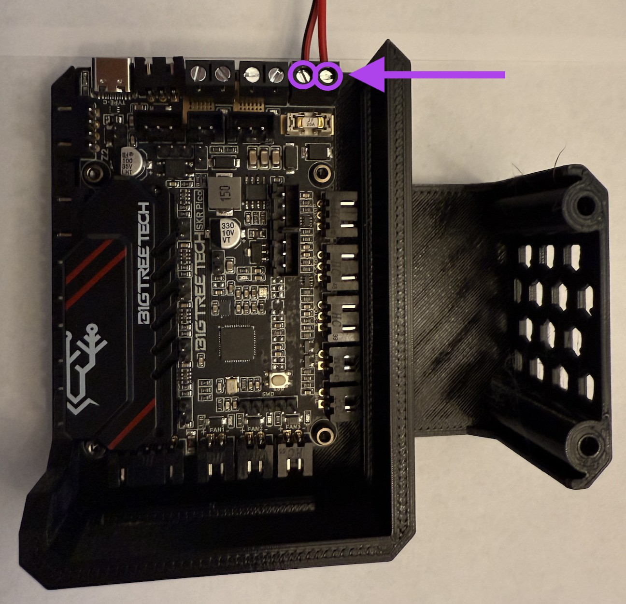
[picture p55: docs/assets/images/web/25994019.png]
    

- Connect the power cables from the PSU to the SKR Pico.

    Prepare the following for this step:

    :red_circle: Power cables and PSU

    :orange_circle: SKR Pico with case

    Flat-head screwdriver

    :green_circle: Loosen both power terminals on the SKR.

    :red_circle: Plug the **red** wire into the **positive** terminal on the SKR.

    :blue_circle: Plug the **black** wire into the **negative** terminal on the SKR.

    :purple_circle: Firmly tighten both power terminals on the SKR.

</div>





###**Step 7** Preparing the 3HOME

<div class="grid cards" markdown>
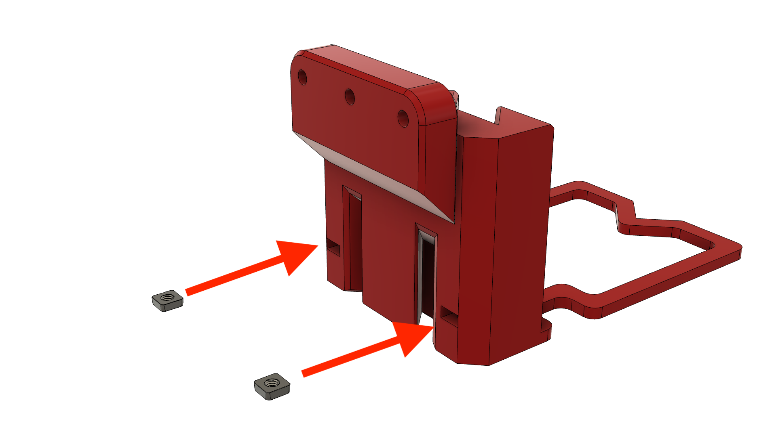
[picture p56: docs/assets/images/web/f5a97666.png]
- 

- Add M3 square nuts to the 3HOME.

    Prepare the following for this step:

    - 3HOME

    - 2x M3nS Square nuts

    :red_circle: Insert the two square nuts into any joiner of the 3HOME

</div>


###**Step 8** Attaching to the 3HOME

<div class="grid cards" markdown>
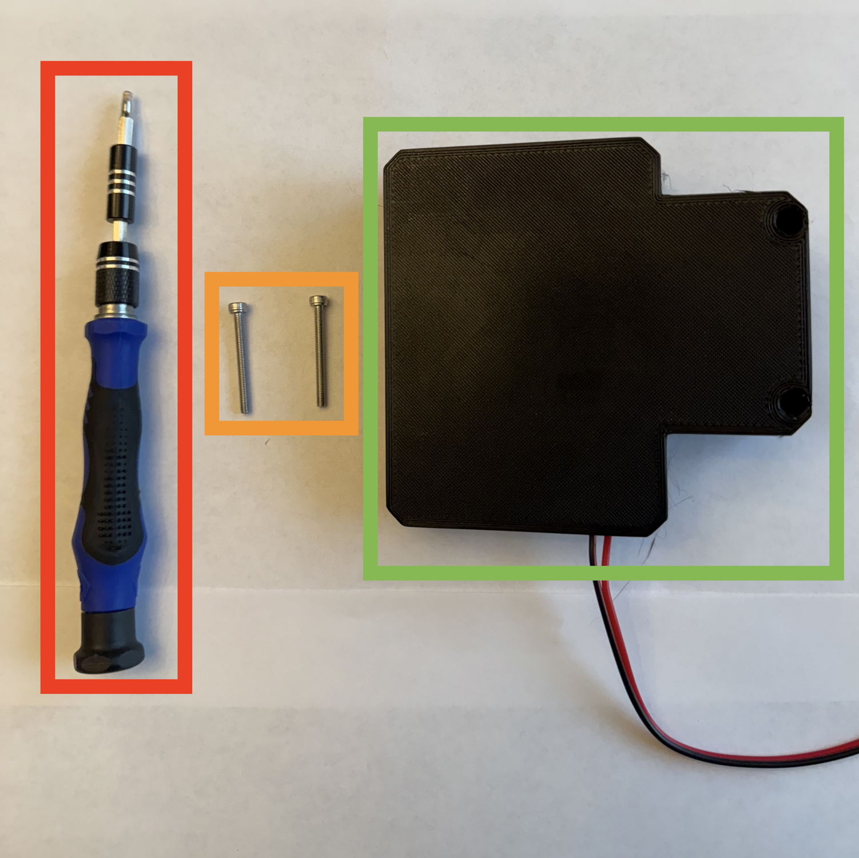
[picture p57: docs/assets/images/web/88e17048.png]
- 
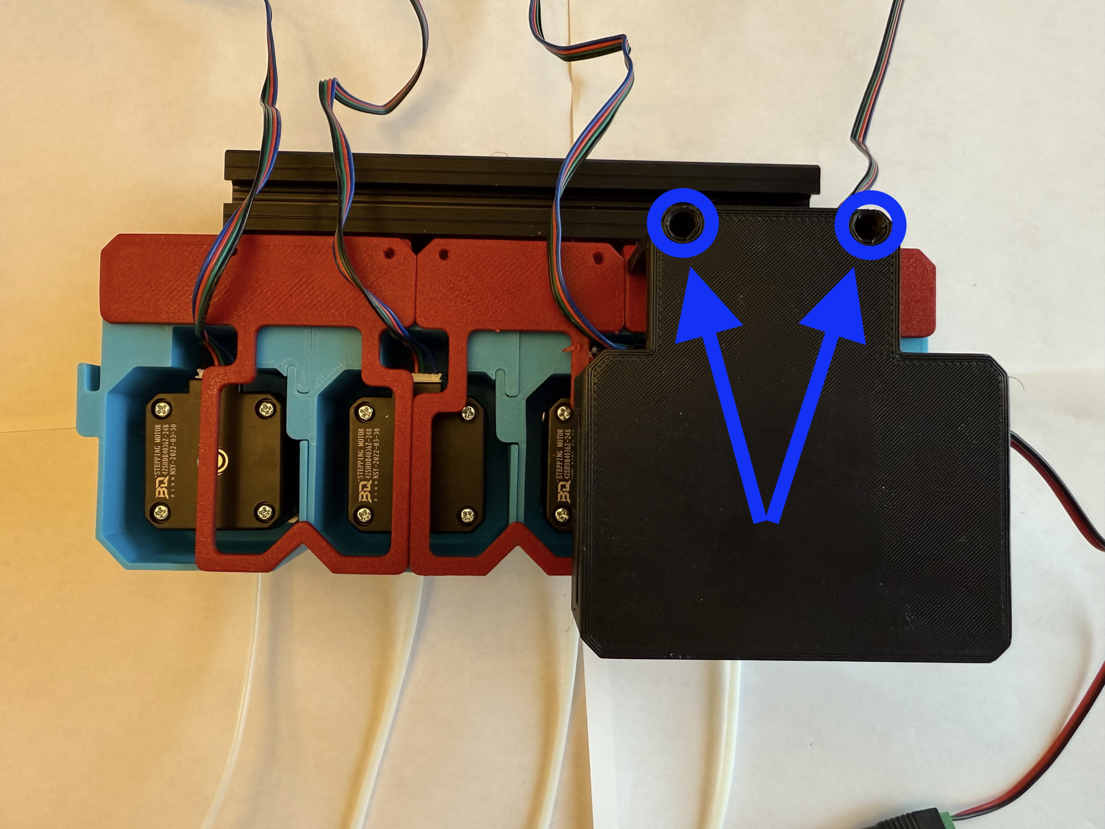
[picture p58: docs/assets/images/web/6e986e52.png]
    

- Attach the SKR Pico case to the 3HOME.

    Prepare the following for this step:

    :red_circle: 2.5mm Hex key

    :orange_circle: 2x M3x30 SHCS

    :green_circle: SKR Pico case (prepared previously)

    :blue_circle: Fasten the SKR Pico to the 3HOME with the two M3x30 SHCS using the 2.5mm hex key.

</div>



###**Step 9** Wire Management

Begin by stretching out each stepper motor wire away from the 3HOME as shown.

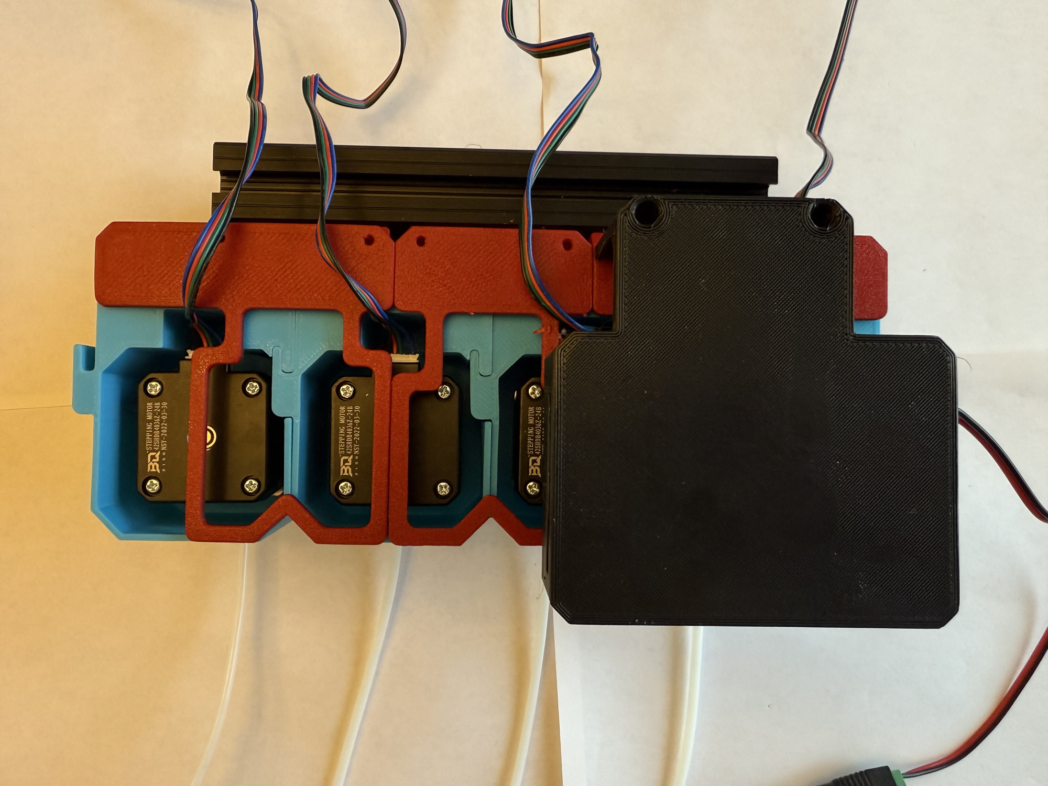
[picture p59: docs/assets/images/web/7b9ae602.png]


Next, take the rightmost wire (T0) and form it into the shape shown.

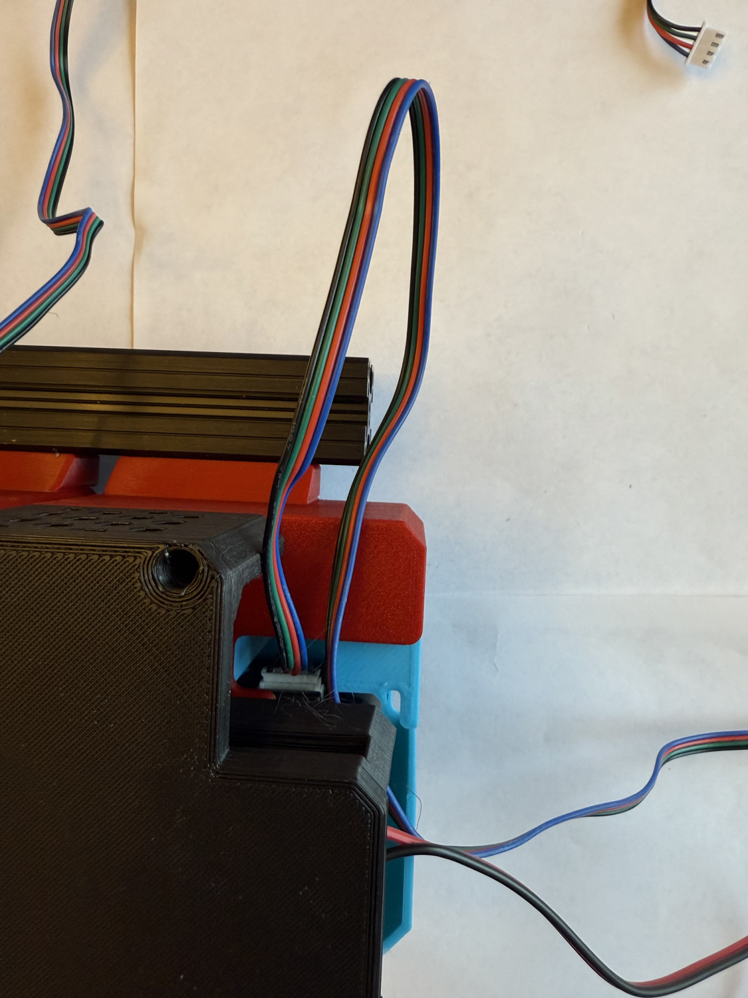
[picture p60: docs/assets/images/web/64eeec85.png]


Fold it back over itself several times until a short length is remaining. Use a zip tie to secure and cut off the excess from the zip tie.

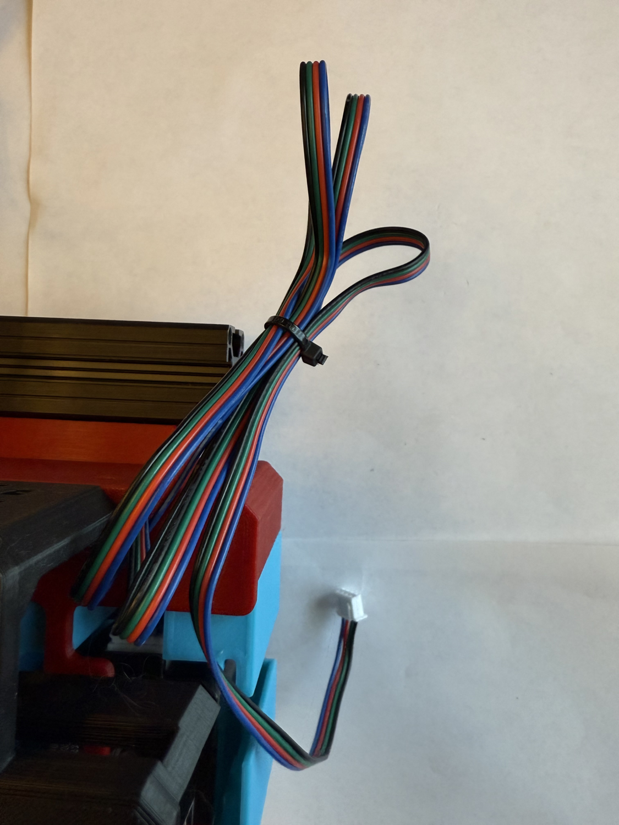
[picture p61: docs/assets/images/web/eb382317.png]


Push the cable bundle into the SKR case and route the wire as shown with the green line.

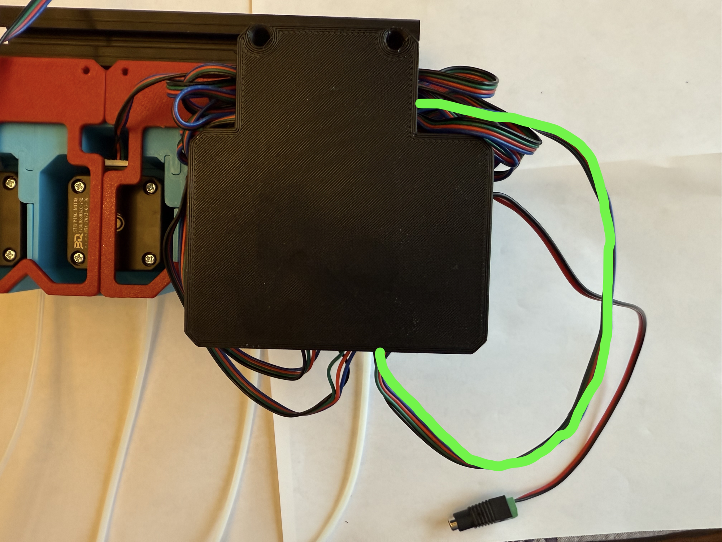
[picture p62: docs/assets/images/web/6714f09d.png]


Plug the stepper cable into the second-to-left port on the SKR (when viewed upside down as shown)

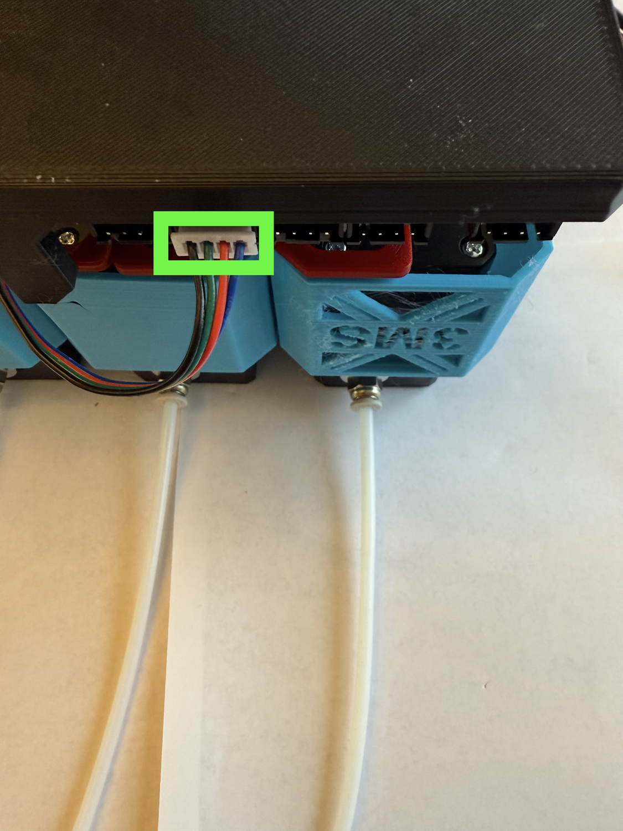
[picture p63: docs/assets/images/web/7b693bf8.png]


Repeat the same process for the stepper motor to the left of the previous one. Plug it into the port to the right of the first one.

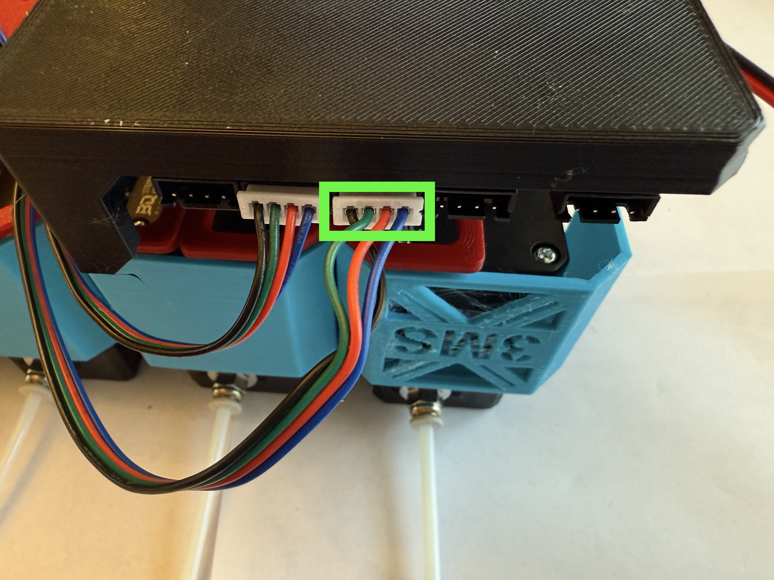
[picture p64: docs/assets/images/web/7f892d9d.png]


Repeat the process for the next stepper motor in line, routing the wire as shown with the green line.

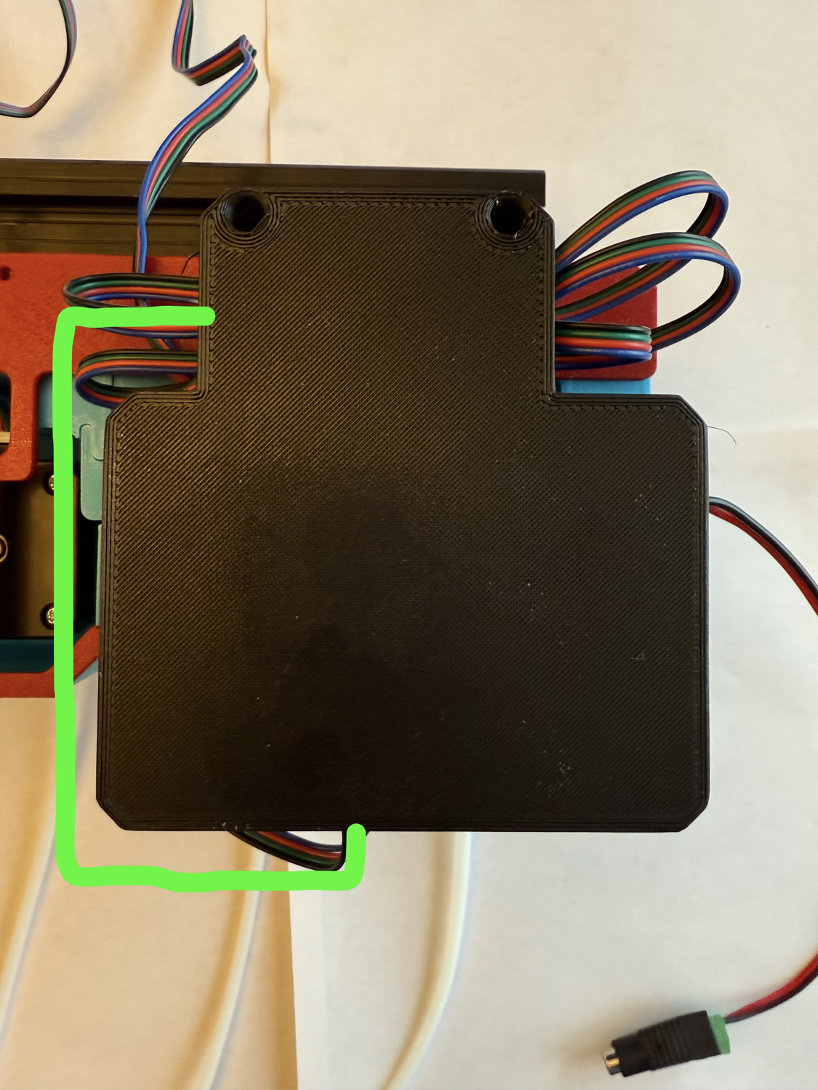
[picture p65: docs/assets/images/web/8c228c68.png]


Plug the stepper into the port to the right of the previous one.

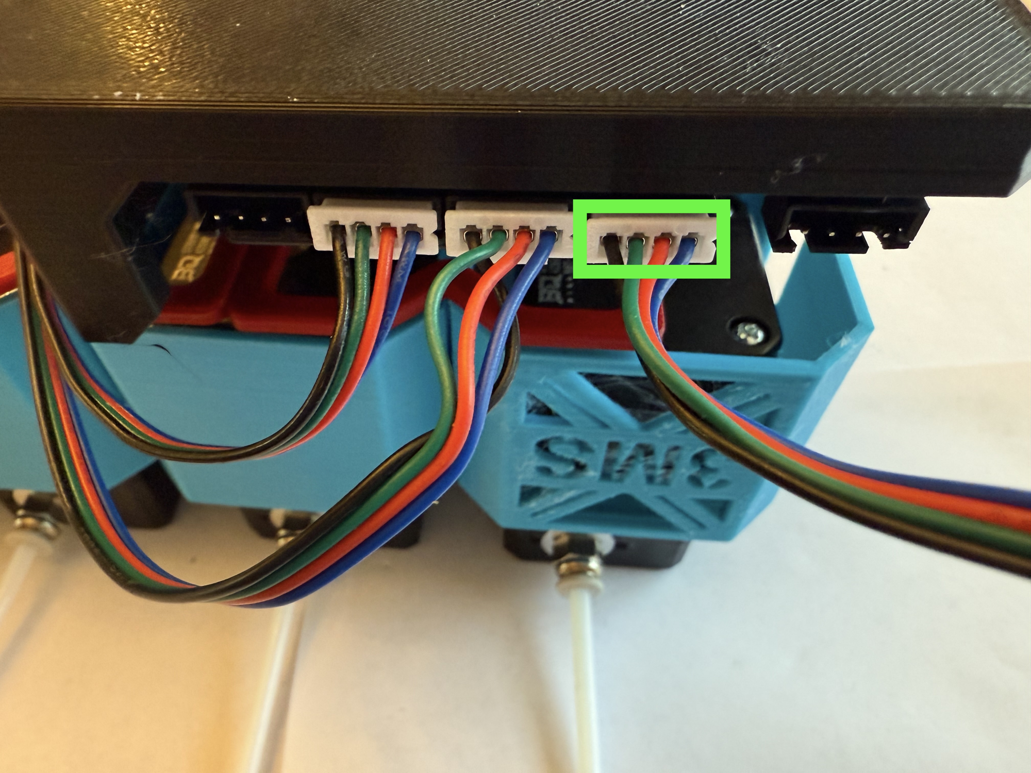
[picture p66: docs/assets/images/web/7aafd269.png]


Repeat the process for the final stepper, routing the wire as shown with the green line.

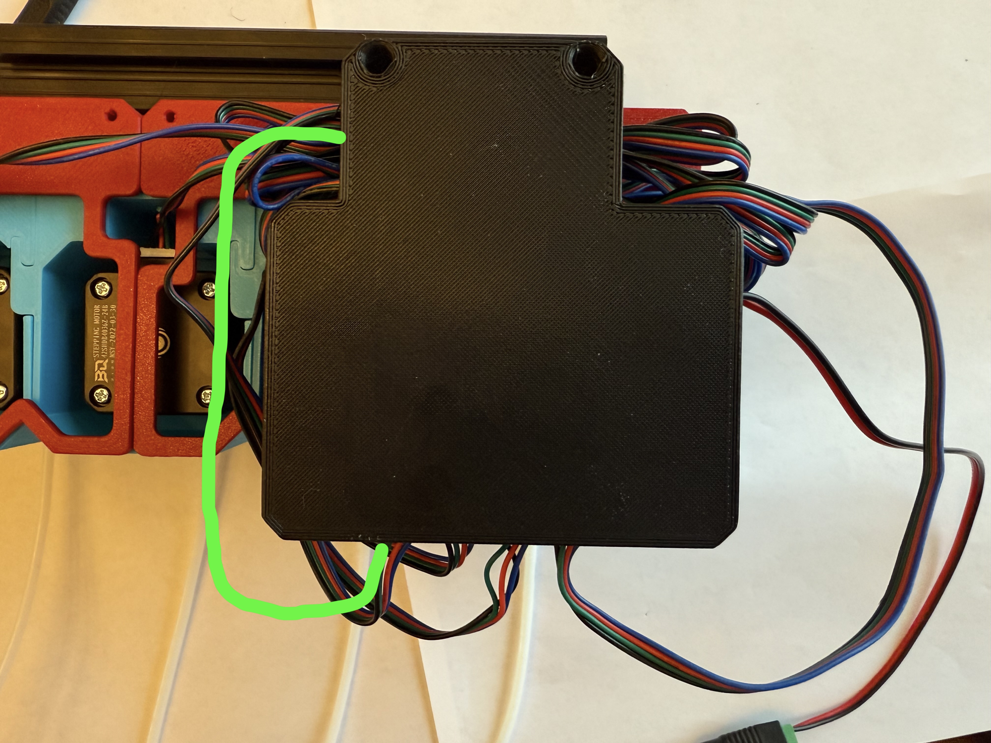
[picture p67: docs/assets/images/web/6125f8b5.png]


Plug this stepper into the leftmost plug on the SKR.

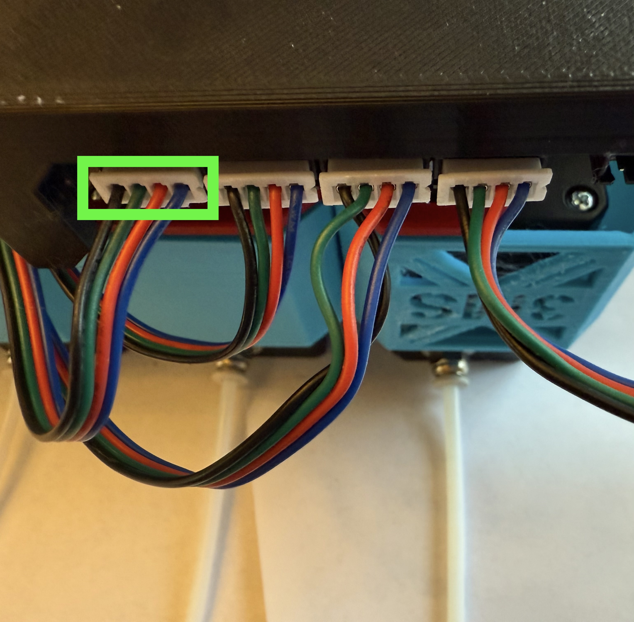
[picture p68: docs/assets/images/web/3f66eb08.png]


:tada: You're done with electronics assembly!

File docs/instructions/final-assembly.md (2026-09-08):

---
comments: true
icon: material/puzzle
---

<link rel="stylesheet" href="../../../assets/css/kits.css">

# Final Assembly

You're almost done with assembling your 3MS! Follow this guide to finish the hardware side of assembly.

###**Step 1** Preparing the PTFE Tubing

<div class="grid cards" markdown>
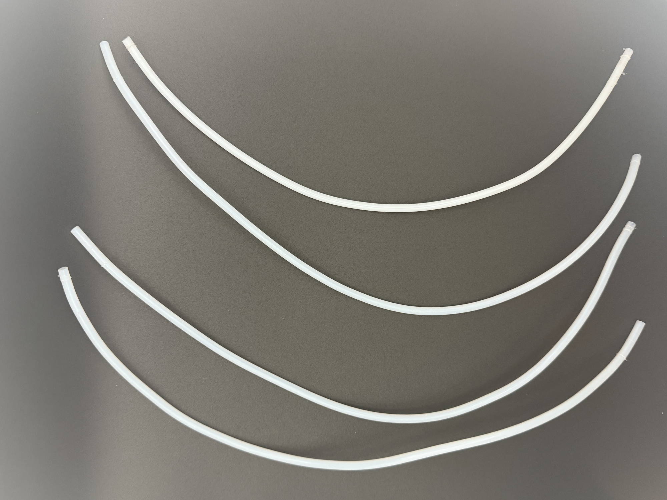
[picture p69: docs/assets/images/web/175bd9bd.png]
- 

- Cut four equal-length segments of PTFE tubing. These should each be long enough to almost reach from the 3MS to your printer's extruder.

</div>


###**Step 2** Inserting the PTFE Tubing

<div class="grid cards" markdown>
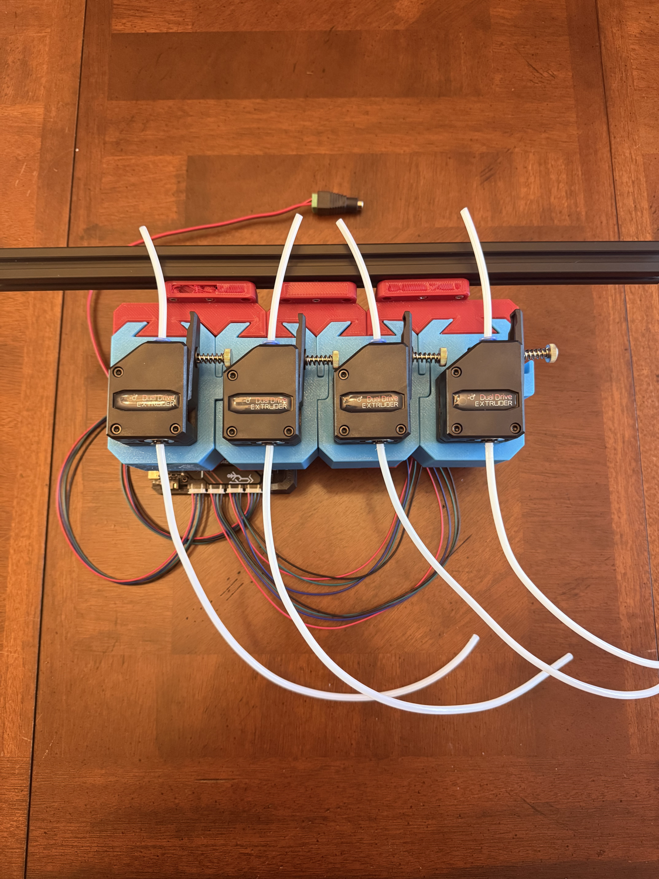
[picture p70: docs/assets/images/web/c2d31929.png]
- 

- Insert all four segments of PTFE tubing into each of the four filament units.

</div>


###**Step 3** Installing the Y-splitter

<div class="grid cards" markdown>
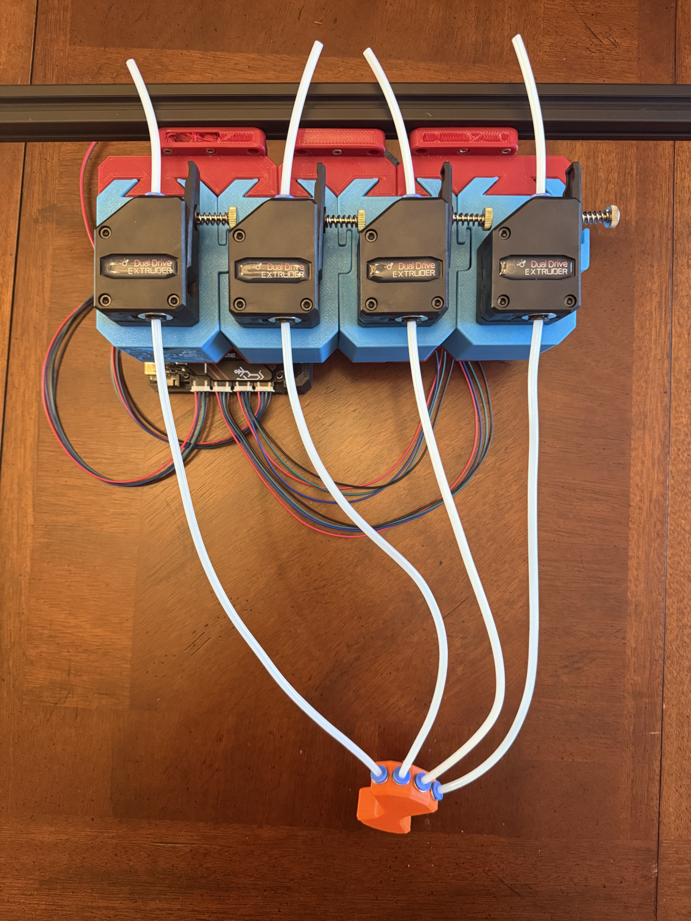
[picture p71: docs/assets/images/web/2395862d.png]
- 

- Insert the other end of each of the four segments of PTFE into the Y-splitter.

</div>


###**Step 4** Tubing to the Extruder

<div class="grid cards" markdown>
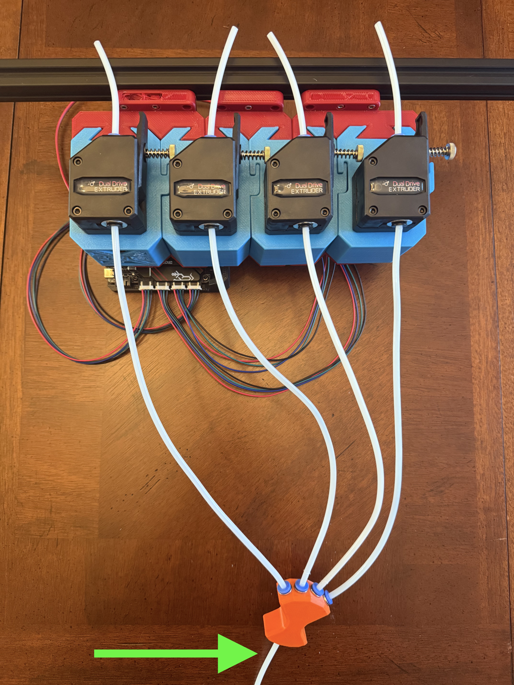
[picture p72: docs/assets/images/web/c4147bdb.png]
- 

- :green_circle: Insert the remaining PTFE tubing into the other end of the Y-splitter. Cut to the proper size to reach your printer's extruder.

</div>


## :tada: You're done building your 3MS!

Please go to [Controllers](../controllers/index.md) to flash firmware for your control board.

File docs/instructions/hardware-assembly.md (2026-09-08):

---
icon: octicons/gear-24
comments: true
---

<link rel="stylesheet" href="../../../assets/css/kits.css">

# Hardware Assembly

!!! info "Important"
    Please note that you must repeat this page four times to assemble all four extruders for your 3MS.

###**Step 1** Locating the Extruders Internals

<div class="grid cards" markdown>
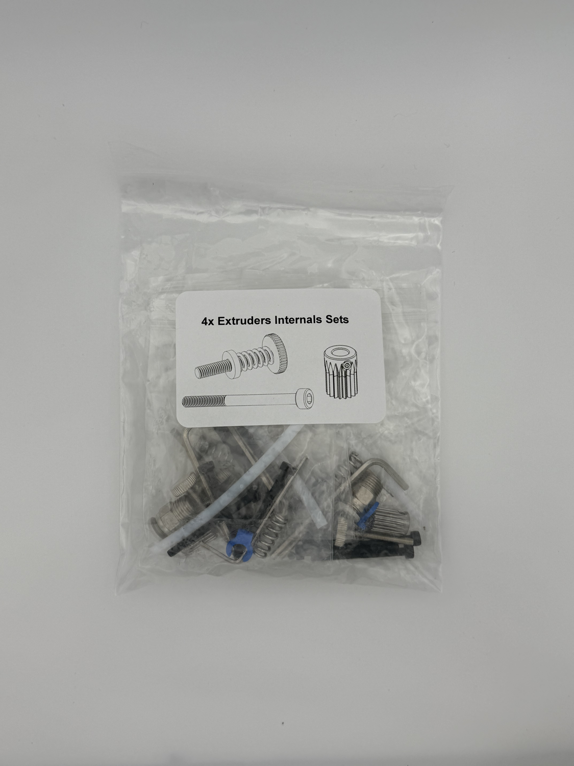
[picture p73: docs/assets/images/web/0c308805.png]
- 
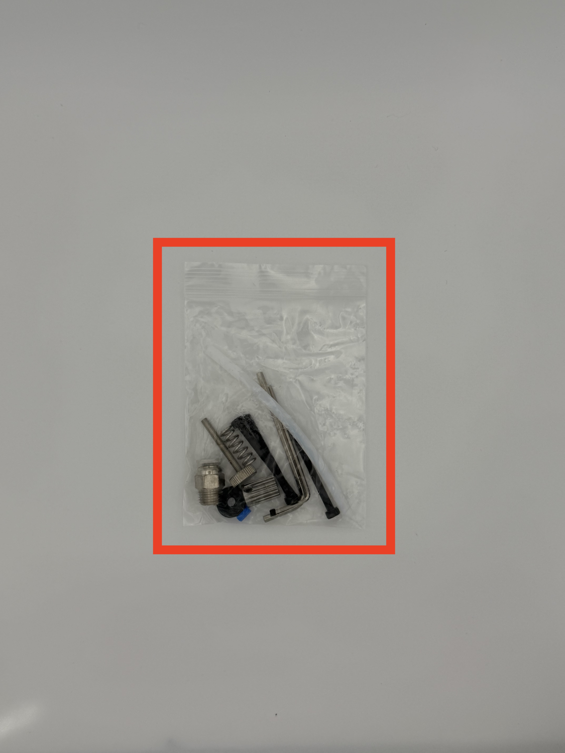
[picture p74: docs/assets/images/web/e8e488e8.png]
    

- Begin by locating the extruders internals set in your 3MS kit.

    :red_circle: Remove one extruder internal set from the bag.

</div>



###**Step 2** Preparing the Stepper Gear

<div class="grid cards" markdown>
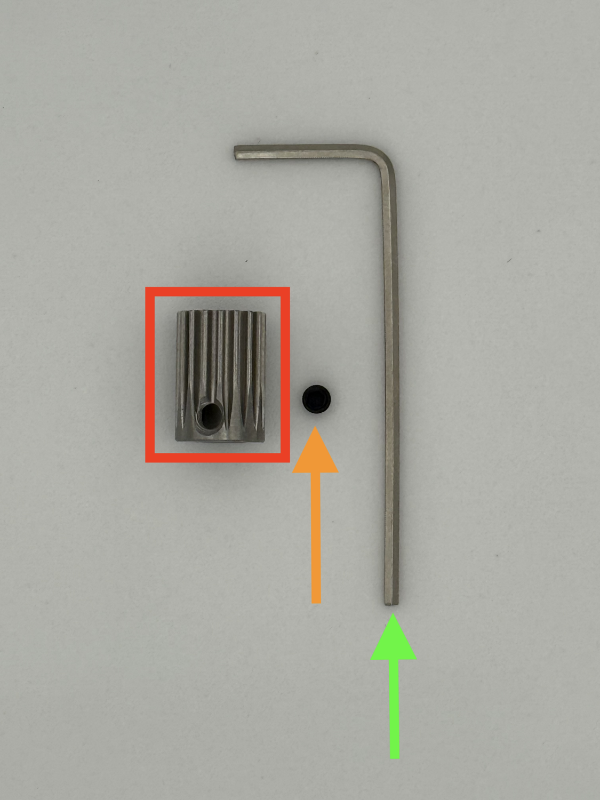
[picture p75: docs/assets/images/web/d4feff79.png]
- 
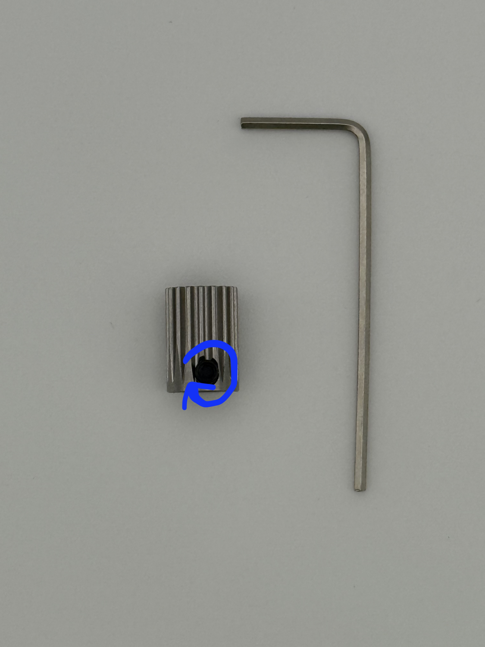
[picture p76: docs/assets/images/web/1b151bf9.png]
    
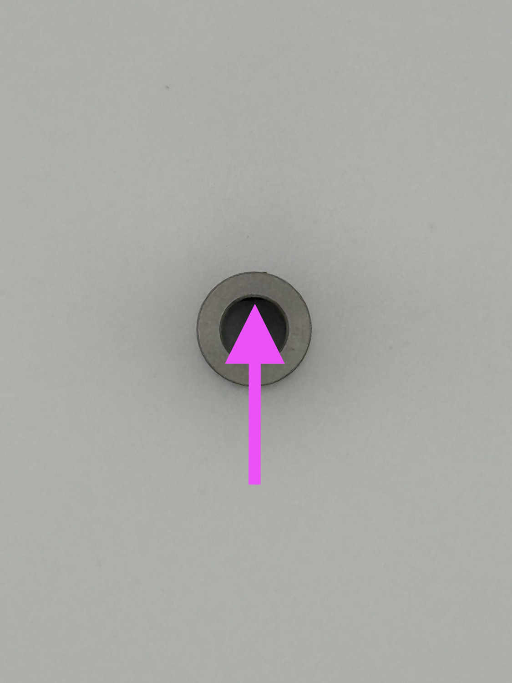
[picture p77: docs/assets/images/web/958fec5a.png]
    

- Prepare the following for this step:

    :red_circle: Stepper gear

    :orange_circle: Stepper gear screw

    :green_circle: 1.5mm Hex key

    :blue_circle: Using the 1.5mm hex key, screw the stepper gear screw into the stepper gear.

    :purple_circle: Ensure the screw is **slightly** sticking into the gear.

</div>




###**Step 3** Attach the Stepper Gear to the Stepper Motor

<div class="grid cards" markdown>
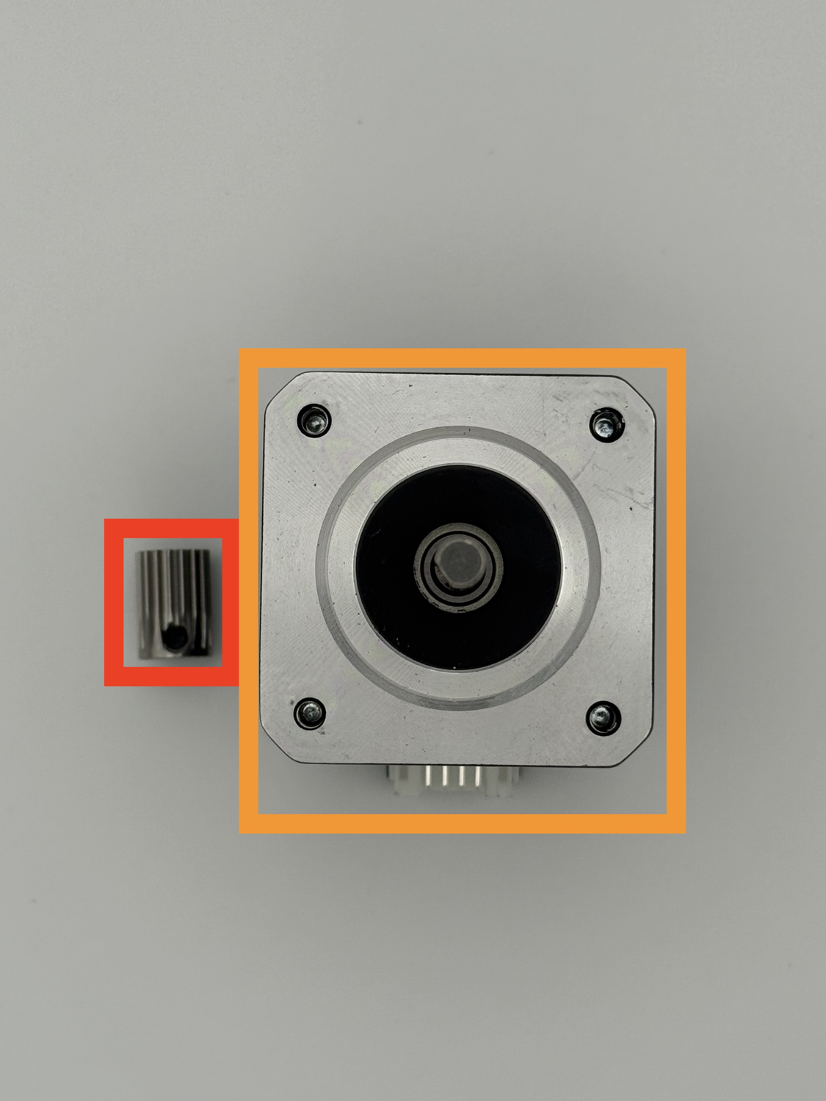
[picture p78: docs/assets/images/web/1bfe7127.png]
- 
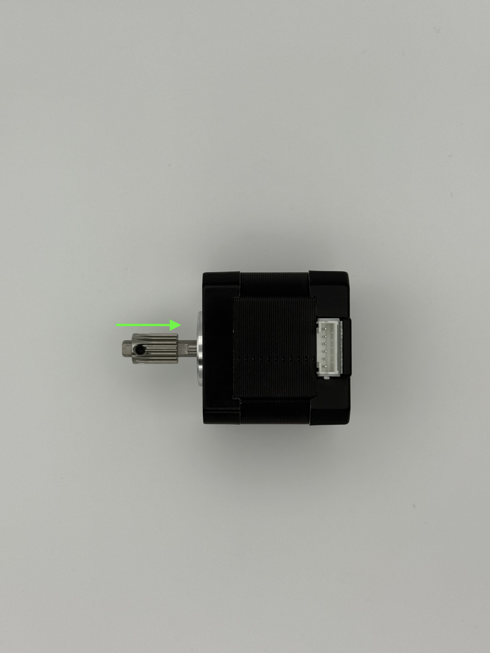
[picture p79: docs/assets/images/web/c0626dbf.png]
    
    
    

- Attach the stepper gear to the stepper motor.

    Prepare the following for this step:

    :red_circle: Stepper gear (prepared previously)

    :orange_circle: Stepper motor

    :green_circle: Slide the stepper gear onto the stepper motor shaft. Note the orientation of the motor. Ensure the stepper gear screw is on the same side as the flat-side of the stepper motor shaft.

    :blue_circle: Slide the edge of the gear to the edge of the stepper motor shaft.

    :purple_circle: Tighten the stepper gear firmly.

    !!! tip "Loctite"
        A bit of blue loctite here can help to ensure the grub screw doesn't work its way loose over time.

</div>





###**Step 4** Filament Unit Parts Preparation

<div class="grid cards" markdown>
- 

- Prepare the following for the next steps:

    :red_circle: Extruder

    :orange_circle: 3x M3x30 SHCS (in extruders internals bag)

    :green_circle: Filament Unit for 3HOME

    :blue_circle: NEMA17 Stepper motor (prepared previously)

    :purple_circle: 2.5mm Hex key

    !!! tip "Lubricant"
        It's recommended to apply a small amount of a lubricant like SuperLube to the white extruder gear.

</div>


###**Step 5** Assembling the Filament Unit

<div class="grid cards" markdown>
- 
    
    

- Assemble the filament unit.

    :red_circle: Place the 3x M3x30 SHCS through the extruder into the filament unit. Note the orientation.

    :orange_circle: Flip the filament unit over and place the NEMA17 stepper motor through the bottom. Note the orientation.

    - Even though the picture doesn't show it, it is recommended to plug the stepper cable before placing the stepper into the 3HOME.

    :green_circle: Flip the filament unit over again and tighten the three M3 bolts.

</div>




###**Step 6** Installing the Tensioner

<div class="grid cards" markdown>
- 
    
    
    
    

- Prepare the following for this step:

    :red_circle: Tension screw (in extruder internals bag)

    :orange_circle: Tension washer (in extruder internals bag)

    :green_circle: Tension spring (in extruder internals bag)

    :blue_circle: Assemble the three as shown.

    :purple_circle: Install the tensioner into the extruder through the hole on the side.

</div>






###**Step 7** Final Extruder Assembly

<div class="grid cards" markdown>
- 
    
    
    

- Prepare the following for this step:

    :red_circle: PC4-M10 fitting

    :blue_circle: Blue Collet clip

    :orange_circle: Locate the hole on the extruder and screw the PC4-M10 fitting into it.

    :green_circle: Insert the short length of PTFE into the ECAS fitting on the opposite end of the extruder.

</div>





### **Make sure to repeat this chapter a total of four times.**

:tada: You're done with extruders assembly!

<!-- [:material-arrow-left: Printed Parts and Tools](printed-parts-and-tools.md){.md-button}

[:material-arrow-right: Electronics Assembly](electronic-assembly.md){.md-button} -->

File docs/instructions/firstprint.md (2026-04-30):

---
comments: true
icon: fontawesome/solid/flag-checkered
description: Slicer setup for the 3MS and other Klipper MMUs with OrcaSlicer.
title: First Print
---

# First Print

Congratulations on building your 3MS! Now to get started with a first print.

## Slicer Setup

This tutorial will walk you through setting up the 3MS with OrcaSlicer. If you use another slicer, some settings may differ.

!!! info "Credit"
    This tutorial is based off of the original Happy Hare slicer setup docs, available [here](https://github.com/moggieuk/Happy-Hare/wiki/Slicer-Setup).

### Machine Settings

Begin by opening your machine settings.



Navigate to `Machine G-Code`.



#### Start G-Code

Prepend your `Machine start G-code` with the following:

```yaml
MMU_START_SETUP INITIAL_TOOL={initial_tool} TOTAL_TOOLCHANGES=!total_toolchanges! REFERENCED_TOOLS=!referenced_tools! TOOL_COLORS=!colors! TOOL_TEMPS=!temperatures! TOOL_MATERIALS=!materials! FILAMENT_NAMES=!filament_names! PURGE_VOLUMES=!purge_volumes!
MMU_START_CHECK
```

Then, append the following below your existing G-code:

```yaml
MMU_START_LOAD_INITIAL_TOOL
; Optionally add YOUR additional start logic (like purging) here to run just prior to start
SET_PRINT_STATS_INFO TOTAL_LAYER={total_layer_count} ; For pause at layer functionality and better print stats
```

#### End G-Code

Prepend your `Machine end G-Code` with the following:

```yaml
MMU_END
```

Then, append the following below your existing G-code:

```yaml
MMU_PRINT_END ; Only required if using Octoprint
```

#### Layer Change G-Code

Scroll down and edit your layer change G-Code.

Add the following:

```yaml
_MMU_UPDATE_HEIGHT

; If you want enhanced pausing feature with Happy Hare client macros also add this
SET_PRINT_STATS_INFO CURRENT_LAYER={layer_num} ; For pause at layer functionality and better print stats
```

Save this machine preset with a new name.

### Filament Settings

!!! tip "Filament Cutting vs. Tip Forming"
    It is recommended you install a filament cutter on your printer. This will make your toolchanges much more reliable and negate the tuning tip forming requires.

    You can find user-submitted tip cutting/forming configurations [here](https://link.3dcoded.xyz/tipconfigs/).

    If you want to do tip forming and can't find the right configs for your setup at the above link, you will have to tune the values yourself. In general:

    - Less cooling moves or higher temperature = stringy tips
    - More cooling moves or lower temperature = blobby tips
    - Skinnydip string reduction = less strings

    Please upload your settings [here](https://link.3dcoded.xyz/tipconfigs/) once you tune yours in so other users can benefit!

Begin by opening your filament settings.



Navigate to `Multimaterial`.



#### Disable Tip Forming

Set all the indicated fields to `0` and open the ramming settings.



Set the ramming time to `0`.



## Your First Print

This section will cover one way to start multicolor 3D prints. Note that typically, multicolor 3D models will come pre-painted or in multiple parts, so the process will be slightly different.

Begin by loading the model into the slicer.



Select the model and click multicolor painting.



Paint the model as you like.



Ensure the prime tower is enabled.



Arrange the prime tower on the plater.



Slice and print!

# :tada:

_I would really appreciate a star on [GitHub](https://github.com/3DCoded/3MS) if you enjoyed this project!_

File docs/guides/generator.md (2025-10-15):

---
comments: true
title: Configuration Generator
icon: material/auto-fix
---

# Configuration Generator

Follow this guide to create a custom configuration for your 3MS.

This has been moved to [https://link.3dcoded.xyz/configgenerator/](https://link.3dcoded.xyz/configgenerator/)

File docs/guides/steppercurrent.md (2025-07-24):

---
title: Tuning Stepper Current
icon: material/tune
comments: true
---

# Tuning Stepper Current

Tuning stepper current is an important part of any 3D printer, including MMU's. Follow this guide to find the optimal `run_current` setting for your 3MS gear steppers.

## Why Tune Stepper Current?

Firstly, why tune stepper current in the first place?

If your stepper current is too **low**, you might notice your stepper skipping when trying to move filament.

If your stepper current is too **high**, you might notice your stepper grinding filament if something is preventing its motion.


/// caption
Grinding filament

Source: Simplify3D
///

---

Follow the below steps to tune your 3MS gear steppers.

## Hardware Limits

Firstly, find the maximum current your stepper can safely run at. There are three main things that can limit this. For this example, components from [3MS Kits](../kits/index.md) will be used.

- PSU rated current. The PSU included in 3MS kits is rated to 2A. The stepper current cannot exceed this.
- Driver rated current. The TMC2209's on the SKR Pico included in 3MS kits are rated to 2A continuous current. The stepper current cannot exceed this.
- Stepper rated current. The steppers included in 3MS kits are rated to 1A. Generally, you don't want to exceed 75% of your stepper's rated current, bringing down our safe limit to 0.75A. The stepper current cannot exceed this.

The lowest of the three values (for this example) is 0.75A. Therefore, your `run_current` cannot exceed 0.75A of current.

### Maximum Current

Now that the maximum safe current for the steppers is known, we can test the stepper at the max current to see if it can drive filament at its max current.

First, set your `run_current` to the maximum calculated previously.

```cfg title="mmu_hardware.cfg"
[tmc2209 stepper_mmu_gear]
run_current: 0.75
```

Restart Klipper.

There are two parts to this test:

1. Free filament test
2. Blocked filament test

## Free Filament Test

Begin by detaching the PTFE from the exit of the 3MS extruder and manually loading filament into the extruder. Next, run in your Mainsail/Fluidd console:

```
MMU_SELECT GATE=0
MMU_TEST_MOVE MOVE=100
```

!!! failure "Operation not possible. MMU has filament loaded"
        If Mainsail reports this error after trying to select a gate, run the following command to tell HH that filament is _not_ loaded.

        ```
        MMU_RECOVER LOADED=0
        ```

Observe the behavior of the stepper. If your stepper moves the filament without any skipping, move onto the next test.

If the stepper skips when it tries to move the filament, there are a couple things you can try:

- Reducing `gear_max_velocity` and/or `gear_max_accel` in `mmu_parameters.cfg`
- Lowering extruder tension by loosening the tension screw

## Blocked Filament Test

Begin by inserting a loose piece of filament into the Y-splitter (blue in the below diagram).



Next, attach PTFE to the end of the 3MS extruder and to another input on the Y-splitter. Load the filament manually through the 3MS extruder until it wedges itself against the loose filament. In the above diagram, the green filament represents the filament in the 3MS extruder.

In the Mainsail/Fluidd console, run:

```
MMU_SELECT GATE=0
MMU_TEST_MOVE MOVE=50
```

If the stepper skips steps, your `run_current` is properly set.

If the stepper grinds the filament, your `run_current` is too high. Reduce it by 0.05-0.1, restart Klipper, and repeat this test until the stepper skips steps.

!!! warning
    Make sure when reducing stepper current that it also passes the [free filament test](#free-filament-test) as well as the [blocked filament test](#blocked-filament-test).

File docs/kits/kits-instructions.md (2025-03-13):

---
comments: true
---

# Instructions for 3MS Kits

Thank you for your purchase of a 3MS kit! Each purchase supports me and my further development of the 3MS and my other open-source projects.

## Chapters

Follow each of these chapters in order to assemble your 3MS.

<div class="grid cards" markdown>
- [:material-tools: 1. Printed Parts & Tools](printed-parts-and-tools.md){.md-button}
</div>

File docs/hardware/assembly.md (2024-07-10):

# Assembly Instructions

Follow this guide to assemble your 3MS.

## Printed Parts

An optional board enclosure for the SKR Mini E3 is available [here](https://www.printables.com/model/459809-bigtreetech-skr-mini-e3-v3-enclosure).

Additionaly, an optional univeral mount for the MK8 extruder using M3 bolts is available [here](../assets/stls/mk8m3.stl). Note that this requires 2-4 M3 bolts and a place to screw the bolts into.

Finally, you will need to print enough of [these](https://www.printables.com/model/541678-bambu-ams-no-catch-y-splitter-pc4-m10) Y splitters for the filament.

## MK8 Assembly

Next, assemble the MK8 extruders onto the NEMA17 motors using the provided instructions that came with them. If you use the mount provided above, make sure it is in between the MK8 and NEMA17. 

## Wiring

After that, route the wires from the NEMA17 to the controller board. Follow this table to determine which port to plug the motors into:

| Filament Unit # | Motor Port |
| - | - |
| 0 | XM |
| 1 | YM |
| 2 | ZAM or ZBM |
| 3 | E0M |

Now, grab your 12V PSU and two M-M duponts, one red and one black (M-M means that there is metal coming out of both ends of the cable). Plug the PSU into the wall, but don't plug the screw terminals into the PSU (the screw terminals have green)

1. Plug the red wire into the positive terminal of the screw termianls
2. Plug the black wire into the negative terminal of the screw terminals
3. Following this image, choose either the DCIN or POWER input

4. Route the two wires inside closest to your chosen input
5. Using the markings on the board, plug the red wire into the positive terminal on the SKR
6. Using the markings on the board, plug the black wire into the negative terminal on the SKR
7. Verify all connections
8. Plug the PSU screw terminals into the PSU wire

If the SKR lights up, you wired it correctly!

Finally, plug the SKR into your Klipper host with the blue cable that came with it.

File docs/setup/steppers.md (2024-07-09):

# Stepper Setup

Follow this guide to calibrate each of the stepper motors. Each of these steps should be repeated for each of your filament units, replacing `TOOL=0` with `TOOL=1`, and so on. Also replacing `3ms0` with `3ms1`, and so on.

!!! info
    If your stepper motor shakes erratically while running any of these commands, your wiring may be incorrect.

## Is the motor spinning?

Run this command:

```gcode
SYNC_TOOL TOOL=0
G1 E50 F4500
```

If the motor spins, skip to the next step. If not, check your wiring first. If your wiring is fine, go to `3ms/steppers.cfg`. Locate the section named `[extruder_stepper 3ms0]`, replacing `0` with the `TOOL` number of the motor not spinning. In front of the `enable_pin`, add, an `!`. If there already is one, remove it. Example:

=== "Before"
    ``` cfg title="3ms/steppers.cfg"
    enable_pin: !arduino: PD7
    ```
=== "After"
    ``` cfg title="3ms/steppers.cfg"
    enable_pin: arduino: PD7
    ```

## Is the motor spinning backwards?

Preload each of the filament units with a piece of scrap filament by pushing the lever to release the tension, inserting filament, then releasing the lever to restore tension. Next, run this command:

```gcode
SYNC_TOOL TOOL=0
G1 E50 F4500
```

Note which way the filament moves. If it moves forwards, away from the PTFE coupler, skip to the last step. If it moves backwards, you have two choices:

- Switch the motor's wires
- Invert the pin in the configuration

To invert the pin in the configuration, locate the configuration section for the filament unit spinning backwards, and invert the `dir_pin`. See the previous section for how to invert the pin.

## How far does the filament move?

This section is a modified version of the [Klipper Docs](https://www.klipper3d.org/Rotation_Distance.html#calibrating-rotation_distance-on-extruders)

Preload each of the filament units with a piece of scrap filament at least 200mm long by pushing the lever to release the tension, inserting filament, then releasing the lever to restore tension.

Use a ruler and a marker to place a mark 70mm from the inlet of the filament unit. Use calipers to measure the actual distance. Write it down, as it will be referred to as `<initial_mark_distance>`.

Next, run this command:

```gcode
SYNC_TOOL TOOL=0
G1 E50 F1500
```

Use calipers to measure the new distance between the inlet of the filament unit and the mark. Write it down, as it will be referred to as `<next_mark_distance>`. 

Calculate `<actual_extrude_distance> = <initial_mark_distance> - <next_mark_distance>`

In the `steppers.cfg` file (located in `3ms/controllers/xxx/steppers.cfg`), locate the configuration section for the current extruder. Example:

```cfg title="3ms/controllers/btt_skr_mini_e3_v2/steppers.cfg"
[extruder_stepper 3ms0]
extruder: extruder
step_pin: 3ms: PB13
dir_pin: !3ms: PB12
enable_pin: !3ms: PB14
microsteps: 16
rotation_distance: 32.8450
```

Note the `rotation_distance` (last line). In this case, it is `32.8450`.

Calculate the new rotation distance: `new_rotation_distance = <rotation_distance> * <actual_extrude_distance> / 50`. 

Round this result to three or four decimal places. Decrease it by 0.005 (this is so that if this result is slightly off, the 3MS filament unit will skip, instead of the printer's extruder stripping the filament during a print). 

Set the new `rotation_distance` in your config. Save it and restart Klipper.

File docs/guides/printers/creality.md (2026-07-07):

---
comments: true
# icon: printers/creality
---

# Creality E3v3 series

## Introduction

The Creality K1 Ender 3 v3 series printers run a heavily modified Klipper and Linux installation. Because of this, setup isn't as straightforward as on a genuine Klipper and Linux install. If you have another printer running mainline Klipper, it is highly recommended to install the 3MS on it instead.

If you would like to use the 3MS on an E3v3, read on.

!!! tip
    Please read every step here carefully. If you run into issues, please reach out on the 3DCoded Discord (link on homepage) and note the step you are having trouble with.

??? warning "Disclaimer"
    I am not responsible for whatever happens to your machine! You proceed at your own risk and understand that you will likely void your warranty by proceeding.

## Instructions

Thank you **@dr-evil-23** for figuring this out!

1. Compile and flash Katapult to your board.

    If you're using an SKR Pico, select `W25Q080 with CLKDIV 2` as the flash chip.

2. Compile Klipper v0.12.0 and flash to your board.

You can follow the rest of the documentation as usual from here.

[Start Here](../../instructions/index.md){.md-button}

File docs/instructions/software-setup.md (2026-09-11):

---
icon: material/console
---

# Software Setup

## Quickstart

Run in SSH:

```sh
curl https://3ms.3dcoded.xyz/install.sh | bash
```

??? note "Piping to Bash"
    If you'd prefer to not pipe to bash, you can clone the script and run it manually:
    ```sh
    wget https://3ms.3dcoded.xyz/install.sh
    ```
    Review the file contents, then run it:
    ```sh
    bash install.sh
    ```

## Detailed Instructions

[https://moggieuk.github.io/Happy-Hare-Doc/GettingStarted-3MS/](https://moggieuk.github.io/Happy-Hare-Doc/GettingStarted-3MS/)

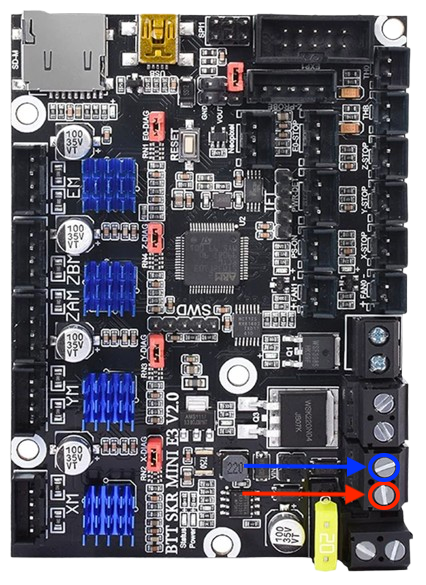
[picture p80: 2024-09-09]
docs/assets/images/assembly/skrminie3v2assembly2.png

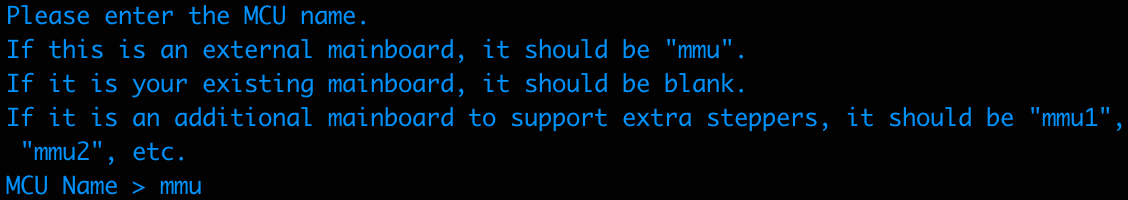
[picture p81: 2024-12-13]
docs/assets/images/guides/generator/generator06.png

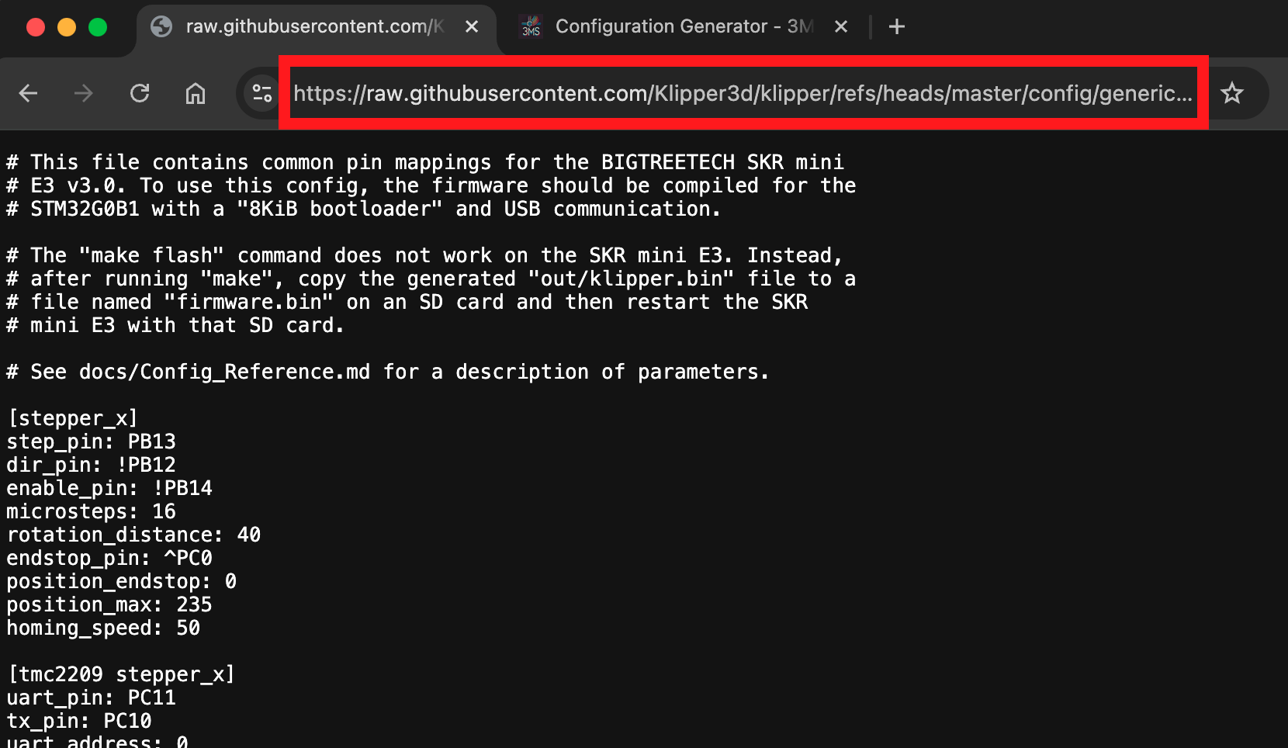
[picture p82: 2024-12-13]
docs/assets/images/guides/generator/generator02.png

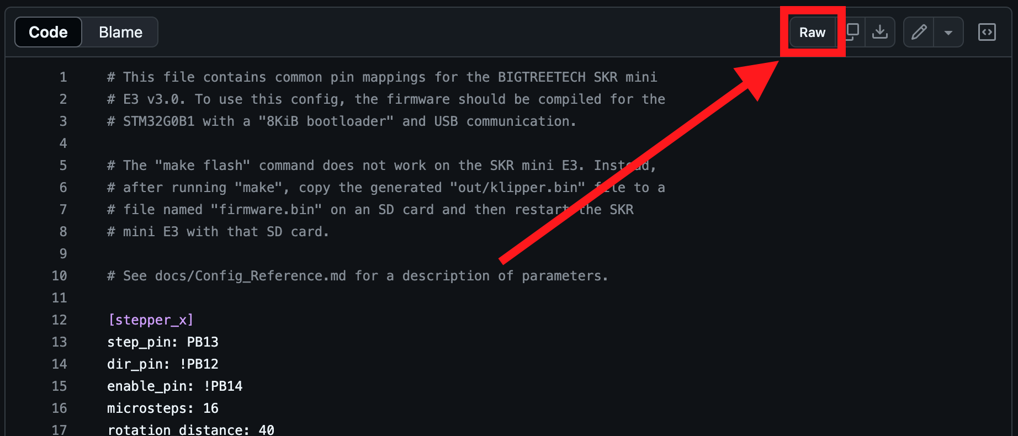
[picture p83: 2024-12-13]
docs/assets/images/guides/generator/generator01.png

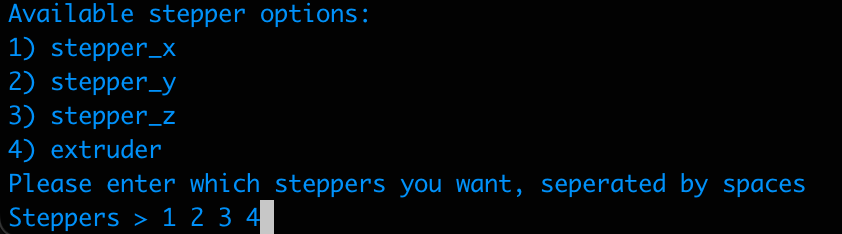
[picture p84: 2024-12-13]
docs/assets/images/guides/generator/generator04.png

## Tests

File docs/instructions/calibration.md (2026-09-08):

---
comments: true
icon: fontawesome/solid/ruler
---

# Calibration

Follow this guide to calibrate your 3MS.

!!! info "Original Documentation"
    This guide is a simplified version of [the official Happy Hare documentation](https://moggieuk.github.io/Happy-Hare-Doc/Calibration/). I highly recommend you read it as it contains useful information and goes more in detail if you are having trouble with the calibrations.

## Verify Filament Sensors

Before calibrating, it is important to ensure that your filament sensors are working properly.

Run in your Klipper console:

```
MMU_SENSORS
```

and verify the output. For each endstop, `open` means no filament detected, and `TRIGGERED` means filament present. Re-run the command several times, inserting/removing filament to each of the sensors, to verify that each filament sensor properly detects filament.

## Gear Steppers

First, calibrate your gear steppers (filament units). The goal of this calibration is to ensure the filament actually moves as far as expected.

First, detach the PTFE tubing from each of the filament units.

For each filament unit (gate), repeat the following steps:

1. Manually load filament until it sticks out slightly from the end of the filament unit
1. Cut the tip of the filament to be flush with the PTFE coupler (side cutters are good for this).
1. Run the following commands in your Klipper console:

    ```
    MMU_SELECT GATE=n
    MMU_TEST_MOVE MOVE=100
    ```

    where `n` is the gate number you are calibrating (starting at zero).

1. The filament should move forwards. If it moves backwards, [invert your gear stepper](#inverting-a-gear-stepper). Measure the distance the filament moved out of the extruder. Using side cutters the same as before can be helpful for this. Run the following command in your Klipper console:

    ```
    MMU_CALIBRATE_GEAR MEASURED=n
    ```

    where `n` is the measured distance.

1. Repeat step **3**. The filament should move exactly `100mm`.

### Tuning the Parking Position (with an extruder entry sensor)

The parking position is the location your filament should park when idle, measured from your gate endstop. This should be set to ~1-2cm above your Y-splitter.

To tune this value, begin by moving the filament in gate 0 to the ideal parking position by hand.



=== "With an extruder entry sensor"
    If you have an extruder entry sensor configured, determining your parking distance from here is super easy.

    Run the following commands in Mainsail:

    ```
    MMU_SELECT GATE=0
    MMU_TEST_HOMING_MOVE MOTOR=gear MOVE=999 SPEED=50 ENDSTOP=extruder STOP_ON_ENDSTOP=1
    ```

    !!! failure "Operation not possible. MMU has filament loaded"
        If Mainsail reports this error after trying to select a gate, run the following command to tell HH that filament is _not_ loaded.

        ```
        MMU_RECOVER LOADED=0
        ```

    Note the distance displayed.

    ```
    Homed after 450.00mm
    ```

    Read your `toolhead_entry_to_extruder` value from `mmu.cfg`

    [Set your parking distance](config.md#parking-position) to:

    ```
    <displayed distance> + <toolhead_entry_to_extruder> + 50
    ```

---

## Inverting a Gear Stepper

If you notice any of your gear steppers moving filament in the opposite direction as expected, you need to invert the gear stepper. There are two options to do this:

- Physically flip the stepper cables
- Invert it in software

To invert a gear stepper in software:

Example, if `T1` is moving backwards:

<video src="/assets/videos/invertstepper.mp4" controls></video>

!!! tip
    If the pin already has a `!` in front of it, remove it to invert it.

Restart Klipper.

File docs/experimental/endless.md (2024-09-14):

---
comments: true
---

# Endless Spool

This feature is based off of [Happy Hare](https://github.com/moggieuk/Happy-Hare) firmware.

!!! info
    The features on this page are experimental.

## Requirements

To use endless spool, your printer must have *one* of the following:

- A filament sensor before your printer's extruder

    !!! success "Recommended"

OR

- A filament sensor before each of the 3MS's extruders

    !!! warning "Untested and deprecated"

The endless spool feature (currently) also only works when printing single-color models.

## Install

To install the endless spool feature, run in your terminal:

```sh
cd ~/3MS
git fetch
git checkout endless-spool
git pull
sh install.sh
```

Update your `3ms/main.cfg`:

```cfg title="3ms/main.cfg" hl_lines="5 9"
[save_variables]
filename: ~/printer_data/config/3ms/variables.cfg

[include ./settings.cfg]
[include ./endless/settings.cfg]
[include ./controllers/btt_skr_mini_e3_v2/steppers.cfg]

[dynamicmacros 3ms]
configs: 3ms/macros.cfg, 3ms/endless/macros.cfg
```

## Usage

To setup endless spool, first choose which filaments can be used as backups for each other. Example with three tools:

- T0 (PLA) -> T1(PLA)
- T1(PLA) -> T0(PLA)
- T2 (PETG) -> PAUSE

In this case, since T0 and T1 are backups for each other, they can be considered in the same "group" and assigned a group number. In this case, `1` will be used. Since T2 doesn't have a backup, it will be its own group. In this case, `2` will be used.

If your printer has a filament sensor before each of the 3MS's filament units, set the `single` setting to `0`. If your printer has only one filamnet sensor before its main extruder, set the `single` setting to `1`.

Edit your `3ms/endless/settings.cfg`:

```cfg title="3ms/endless/settings.cfg" hl_lines="2-4 6"
[gcode_macro ENDLESS_SETTINGS]
single: 1 # <-- Set to 0 if you have a filament sensor before each of your 3MS extruders. Set to 1 if you have one filament sensor right before your printer's extruder.
variable_t0: 1
variable_t1: 1
### --- Uncomment below for more than two tools --- ###
variable_t2: 2
# variable_t3: -1
gcode:
    RESPOND MSG=""
```

## Filament Sensors

If you have multiple filament sensors, change your filament sensors' `runout_gcode` to:

```cfg
ENDLESS_RUNOUT T=0
```

For the filament sensor associated with T1, change the code from `T=0` to `T=1`, and so on.

---

If you have one filament sensor, change your filament sensor's `runout_gcode` to:

```cfg
ENDLESS_RUNOUT
```

## PRINT_START

In your slicer's print start GCode, add the following parameter to your `PRINT_START` macro:

```
NUM_TOOLCHANGES=[total_toolchanges]
```

Next, in your `PRINT_START` macro, add the following line **before** your `MMMS_START` call:

```
ENDLESS_START NUM_TOOLCHANGES={params.NUM_TOOLCHANGES}
```

This will ensure that Endless Spool is only enabled for single-color prints.

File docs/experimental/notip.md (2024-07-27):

# Toolchanges Without Tip Shaping or Filament Cutter!

Because the 3MS is synchronized to the printer's extruder, it can potentially toolchange without any tip shaping or filament cutter.

!!! info
    This page, and the features mentioned on it, are in develpment

???+ "Development Status"
    So far, the following work without tip shaping:
    
    - [X] Toolchanges without tip shaping
    - [X] Print start/end routines without tip shaping
    - [X] Small prints without tip shaping (up to 5 toolchanges)
    - [X] Medium prints without tip shaping (over 50 toolchanges)
    - [X] Long prints without tip shaping (over 100 toolchanges)
    - Common materials:
        - [X] PLA
            - [X] PLA+
            - [X] High Speed PLA
            - [ ] Silk PLA
        - [ ] PETG
        - [ ] TPU (see [Dual Drive 3MS Extruders for TPU](dualdrivetpu.md))

## Speed Benefits

!!! info
    This section is under construction.

## Should Tip Shaping be Used?

See [Materials](materials.md) for information on whether or not tip shaping should be used for your filaments.

## Slicer Setup

Setup your slicer for no tip shaping as follows.

### Disable Filament Ramming

Disable filament ramming in `Filament Settings` -> `Multimaterial` -> `Toolchange parameters with single extruder MM printers`:

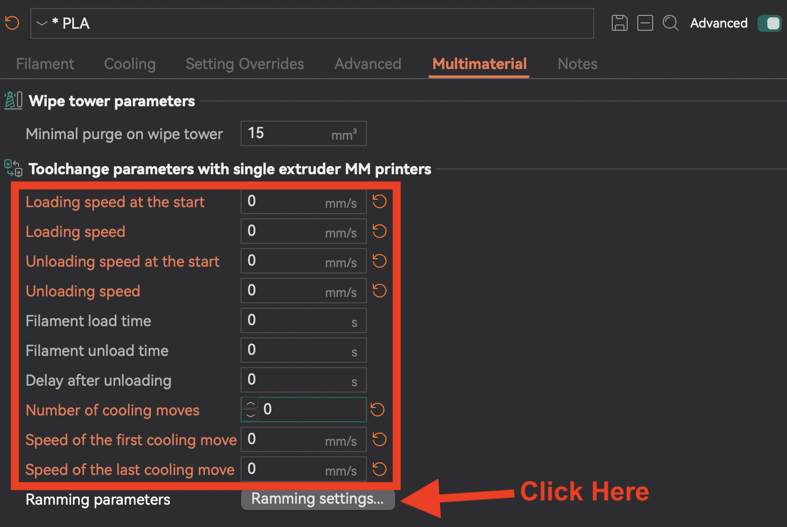
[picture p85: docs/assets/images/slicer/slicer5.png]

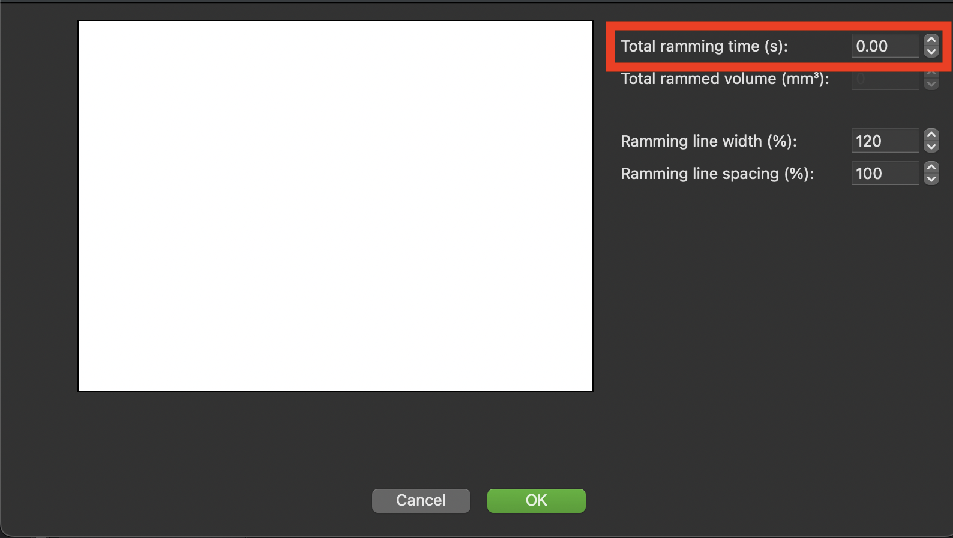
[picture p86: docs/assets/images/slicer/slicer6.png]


### Unload/Load Speed

Next, change the `Unloading speed at start` and `Unloading speed` to 300 (faster is better here). Next, change the `Loading speed at start` and `Loading speed` to 300 and 100, respectively.

???+ info "What this does"
    The main idea behind toolchanges without tip shaping relies on the filament being unloaded too fast to form a blob. Setting the `Unloading speed` settings allows this. Next, loading the filament back can be generally optomized by increasing the `Loading speed` settings.

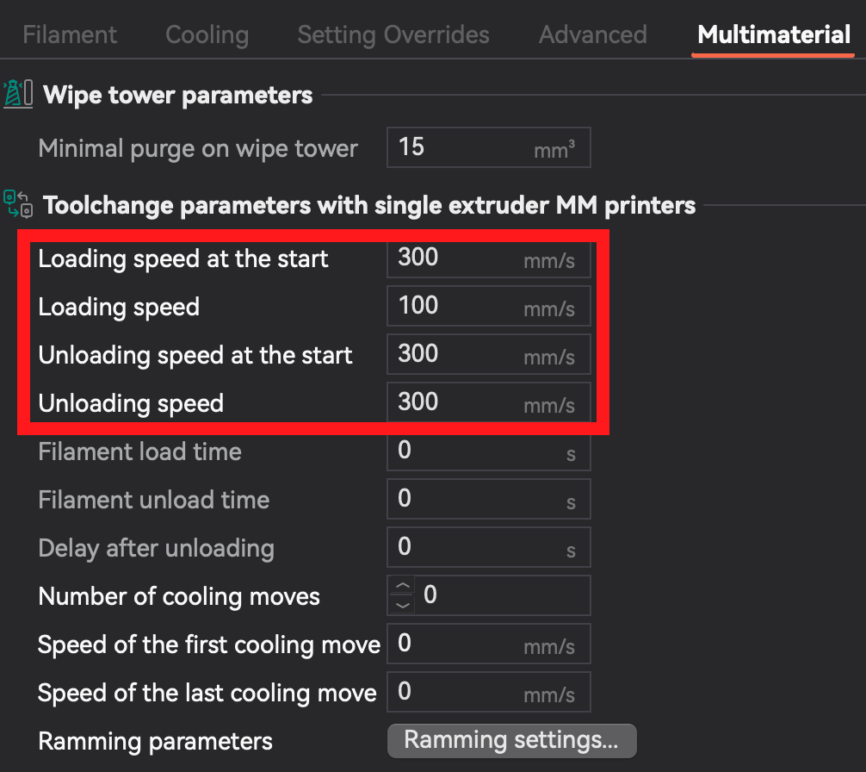
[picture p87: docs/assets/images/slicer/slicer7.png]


### Temperature

If your filament has very long strings on the end of them after unloading without tip shaping (longer than 2cm), decrease your filament temperature. 

If your filament tip has a nearly flat tip, increase your filament temperature.

The ideal filament tip has a pointy end and a small string (less than 5mm). When in doubt, it is recommended to aim for a slightly stringy tip over a flat tip.

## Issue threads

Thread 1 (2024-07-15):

Einsy Rambo (main MCU) to run 3MS Steppers

3DCoded, 2024-07-15:
**Controller Information:**
 - Einsy Rambo
 - [Pinout](https://github.com/ultimachine/Einsy-Rambo/blob/1.1a/board/Project%20Outputs/Schematic%20Prints_Einsy%20Rambo_1.1a.PDF)
 - [Generic Klipper config](https://github.com/Klipper3d/klipper/blob/master/config/generic-einsy-rambo.cfg)

**Important information:**
For the Prusa MK3S+, the Einsy Rambo is still the main MCU, but could be used to run the 3MS steppers, while the SKR Mini E3 V2 is used to run the printer's steppers (quieter operation)

3DCoded, 2024-07-22:
This setup has now been tested enough to consider it no longer experimental. This is still an expert only modification and documentation will be provided soon.

3DCoded, 2024-08-13:
This setup has been tested for around 150 hours, and documentation is now complete.

Closed 2024-08-13.

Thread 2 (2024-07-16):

Spare stepper plugs on BTT Octopus

florek41, 2024-07-16:
It would be useful to document the possibility of using the current/existing mainboard, as it only requires free space for stepsticks, making it much cheaper to set up.

Example:
I have a BTT Octopus on my printer and I'm currently using only 4 of the 8 available steppers, so there is no need to purchase a separate controller for 3MS.

3DCoded, 2024-07-16:
Since each mainboard has a different Klipper configuration, I've renamed this one to be specific to the BTT Octopus. I just updated the documentation and created a configuration for it. Something to note (this is in the documentation) is that you need a TMC2209 for each of the motor ports.

3DCoded, 2024-08-13:
@florek41 Let me know if there's anything I should change in the config for your setup.

3DCoded, 2024-09-11:
Closing this issue as its been open for 30 days with no activity. If this isn't resolved, feel free to reopen this.

Closed 2024-09-11.

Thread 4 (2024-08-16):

ZM3E4 controller (main MCU)

kaiatkins, 2024-08-16:
3D Printer ZoneStar Z9V5 Pro

Controller: ZM3E4

https://github.com/ZONESTAR3D/Control-Board/tree/main/32bit/ZM3E4

Configs:

https://github.com/Z9V5PRO/Z9V5Pro-MK4-Klipper

<Printer.cfg>

[printer]
kinematics: corexy
max_velocity: 300
max_accel: 3000
max_z_velocity: 25
max_z_accel: 30

[stepper_x]
step_pin: PE1
dir_pin: !PE2
enable_pin: !PE0
microsteps: 16
rotation_distance: 20
endstop_pin: !PC13
position_endstop: 0
position_max: 300
homing_speed: 50
homing_retract_dist: 10
second_homing_speed: 10.0

[stepper_y]
step_pin: PE5
dir_pin: !PE4
enable_pin: !PE6
microsteps: 16
rotation_distance: 20
endstop_pin: !PE3
position_endstop: 0
position_max: 300
homing_speed: 50
homing_retract_dist: 10
second_homing_speed: 10.0

[stepper_z]
step_pin: PD3
dir_pin: PD4
enable_pin: !PD2
microsteps: 16
rotation_distance: 4
position_endstop = -1.220
endstop_pin: !PD7
position_min: -20
position_max: 400
homing_retract_dist: 0
second_homing_speed: 8.0

[stepper_z1]
step_pin: PC12
dir_pin: PD0
enable_pin: !PC11
endstop_pin: !PD1
microsteps: 16
rotation_distance: 4

[screws_tilt_adjust]
screw1: 2, 16.5
screw1_name: front left screw
screw2: 293,16.5
screw2_name: front right screw
screw3: 293,286.5
screw3_name: rear right screw
screw4: 2,286.5
screw4_name: rear left screw
horizontal_move_z: 10
speed: 50
screw_thread: CW-M4

[extruder]
step_pin: PD10
dir_pin: !PD9
# change PD9 -> !PD9
enable_pin: !PD11
microsteps: 16
rotation_distance: 7.71
gear_ratio: 50:17
nozzle_diameter: 0.400
filament_diameter: 1.750
heater_pin: PC5
sensor_type: Generic 3950
# NTC 100K B3960 (used)
sensor_pin: PC2
min_temp: 0
max_temp: 250
max_extrude_only_distance: 500
max_extrude_cross_section: 5
control = pid
pid_kp = 18.853
pid_ki = 0.539
pid_kd = 164.732

[verify_heater extruder]
check_gain_time:999999

[heater_fan hotend_fan]
pin: PB8
max_power: 1.0
fan_speed: 1
kick_start_time: 0
heater: extruder
heater_temp: 60.0

[heater_bed]
heater_pin: PA2
sensor_type: EPCOS 100K B57560G104F
sensor_pin: PC3
control = pid
pid_kp = 74.758
pid_ki = 1.181
pid_kd = 1183.043
min_temp: 0
max_temp: 80

[fan]
pin: PB1
max_power: 1.0

<multi_extruder.cfg>

[extruder_stepper extruder_1]
extruder:
step_pin = PD13
dir_pin = !PD12
enable_pin = !PD14
microsteps: 16
rotation_distance: 7.71
gear_ratio: 50:17

[extruder_stepper extruder_2]
extruder:
step_pin = PC6
dir_pin = !PD15
enable_pin = !PC7
microsteps: 16
rotation_distance: 7.71
gear_ratio: 50:17

[extruder_stepper extruder_3]
extruder:
step_pin = PA8
dir_pin = !PC9
enable_pin = !PC10
microsteps: 16
rotation_distance: 7.71
gear_ratio: 50:17

3DCoded, 2024-08-16:
I've added support for the ZM384 [here](https://3dcoded.github.io/3MS/setup/controllers/zm384main/). Due to some quirks with Klipper, as of now, only three extruders will work with the 3MS, and the fourth one will be used as the main extruder.

kaiatkins, 2024-08-16:
Wow that was fast :) Thank you. I have ordered some parts for my machine and will be reworking it.

I plan on using the bambulabs splitter and attach to the hotend.

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

is the ok?

3DCoded, 2024-08-16:
That splitter looks good, but you can also print [this one](https://www.printables.com/model/541678-bambu-ams-no-catch-y-splitter-pc4-m10).

3DCoded, 2024-08-21:
The spitter I previously linked is no longer recommended for setups with more than two filament units (you would need three of those splitters). For a system like yours, [this one](https://www.printables.com/model/122982-mini-splitter-v2-for-mmu21s-mod-pc4-01-fitting-ver) is now recommended (you only need one of these splitters).

kaiatkins, 2024-08-24:
The ZoneStar Z9v5 printer has 4 BMG extruders on the back and feeds either into the company's 4 in 1 out (mixing hotend) or 4 in 1 out (non- mixing hotend) but they lack in quality. So I have switched to klipper and wanted the option to change the hotend into a Bowden single E3D v6 then use like the bambulabs AMS.
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

3DCoded, 2024-08-24:
The 3MS will work fine on an E3D v6 hotend. I recommend getting the splitter as close to the hotend as possible for the speed of tool changes.

kaiatkins, 2024-08-25:
What would be the optimal location for the filament sensor? Currently its the red on the back of the machine.

3DCoded, 2024-08-25:
The optimal location for the filament sensor is between the splitter and the hotend.

kaiatkins, 2024-08-26:
I picked up on sale this (SFS 2.0) that I will use. Once everything arrives, I will start :) thank you for your quick responses, guidance and support 👍
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

3DCoded, 2024-09-20:
@kaiatkins, is the configuration working for you? If not, can you explain what's happening so I can fix it?

kaiatkins, 2024-09-20:
I was just coming on to let you know, I am still waiting for 1 part I ordered to put together then will be ready to go. Thanks for checking in, I am excited to convert to 3MS :)

kaiatkins, 2024-10-07:
package for hotend lost in transit so seller is resending :(

kaiatkins, 2024-10-20:
hello, it has finally arrived and I have started to put the stuff together. I will make mount for the sensor and 4 to 1. I'm contemplating moving the BMG to the top back of the machine instead of the default install, so I can cut out some of the Bowden tube.

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

warm regards from Cambodia 🇰🇭

kaiatkins, 2024-10-22:
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
 Slowly getting there :)

3DCoded, 2024-10-22:
Thank you for keeping track of your build here. I'm sure it will help other people using a similar setup.

kaiatkins, 2024-10-27:
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

So it looks like I’m working with mainboard ZM3E4 v2.1 with TMC2225’s

Are the steppers ok to use or should I replace with 2209s? I don’t see UART so looks like stand-alone.

I am flashing klipper and installing the configuration as it comes with marlin natively

here is the flash information

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

kaiatkins, 2024-10-27:
For my Klipper I use biqu pi which also use it for 2 machines
printer_3MS_data
printer_GEMINI_data

the klipperscreen is controlled in

/home/biqu/.config/KlipperScreen/KlipperScreen.conf

so I need to make sure I save the info to switch between the 2 printers

kaiatkins, 2024-10-27:
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

Dynamic Macros is giving me issue about path

I tried
~/printer_3MS_data/config
and full path
 /home/biqu/printer_3MS_data/config

kaiatkins, 2024-10-27:
Error loading template 'CHECK_FSENSOR': jinja2.exceptions.TemplateAssertionError: no filter named 'str'

I changed
variable_fsensor_name: "**switch_sensor**" # name of filament_switch_sensor right before printer's extruder
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

kaiatkins, 2024-10-27:
I am also getting error

Option 'config_path' is not valid in section 'dynamicmacros'

[dynamicmacros]
config_path: ~/printer_3MS_data/config # If you left your printer configuration path as the default, you don't need to specify this
configs: dynamic.cfg

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

3DCoded, 2024-10-27:
> Option 'config_path' is not valid in section 'dynamicmacros'

You no longer need to specify this option. DynamicMacros automatically finds the correct configuration path for your Klipper instance.

kaiatkins, 2024-10-27:
I was just following https://3dcoded.github.io/DynamicMacros/setup/ and copied it from there, but looks fine now since I removed

when I do sudo service klipper restart

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

3DCoded, 2024-10-27:
Thank you for catching that. I've updated the documentation to remove that option.

> when I do sudo service klipper restart

Just restart your Klipper however you usually do, just not the `RESTART` command. You can do this from the power menu in Mainsail.
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

kaiatkins, 2024-10-27:
Testing the Dynamic Macros

If you run the command MYTEST, the output should be:  Hi! (Works)
Then I go back in file and change to Hi, Bong!, save no restart  Hi! (No Update)
but if I run DYNAMIC_MACRO then MYTEST Hi, Bong! (Works)

3DCoded, 2024-10-27:
Yes. That's expected behavior. `DYNAMIC_MACRO` reloads the macros without restarting Klipper.

kaiatkins, 2024-10-27:
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

What I was showing by following that,

Save the file, but do not restart Klipper.

Run MYTEST again, it didnt update until I manually ran DYNAMIC_MACRO

kaiatkins, 2024-10-27:
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

here is the log after I reenabled 3MS
[klippy.log](https://github.com/user-attachments/files/17533903/klippy.log)

3DCoded, 2024-10-27:
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

Sorry for the confusion. That was a typo, and I just fixed it.

> Error loading template 'CHECK_FSENSOR': jinja2.exceptions.TemplateAssertionError: no filter named 'str'

Can you try updating the 3MS using [this](https://3dcoded.github.io/3MS/instructions/#8-updating)?

kaiatkins, 2024-10-29:
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

did update but still fsensor issue

kaiatkins, 2024-10-29:
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
:) getting there... but I do keep seeing Unknown command:"SET_TOOL_SYNC"

I pressed the macros just to see what would happen and some came up with errors ( I understand the extruder not up to temperature ones others not so sure)

so adding Klipper.log
[Uploading klippy.log…]()

will start calibration for each of the extruders and get back to you

thanks again for your quick responses and fixes

3DCoded, 2024-10-29:
Your log file didn't fully upload. Can you manually edit `3ms/macros.cfg` and use the find tool to find `|str` in the `CHECK_FSENSOR` macro and replace it with `|string`?

kaiatkins, 2024-10-29:
> Your log file didn't fully upload. Can you manually edit `3ms/macros.cfg` and use the find tool to find `|str` in the `CHECK_FSENSOR` macro and replace it with `|string`?

I got the str error corrected by following what you sent before ( the update and then install.sh)

I did reupload the log that has the Unknown command:"SET_TOOL_SYNC" incase you want to look

3DCoded, 2024-10-29:
Can you please upload your config folder as a zip?

kaiatkins, 2024-10-30:
[bd-3ms-configs.zip](https://github.com/user-attachments/files/17565878/bd-3ms-configs.zip)

3DCoded, 2024-10-30:
I think I found the issue. The section `[gcode_macro SET_TOOL_SYNC]` is indented by one space. You can either unindent the following lines in `3ms/macros.cfg`:

```
[gcode_macro SET_TOOL_SYNC]
gcode:
```

or update the 3MS configuration.

kaiatkins, 2024-11-01:
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
 been working on printing out the hotend pieces and finishing off the hardware things

3DCoded, 2024-11-03:
So far your build looks great!

I'm currently working with the developer of [Happy Hare](https://github.com/moggieuk/Happy-Hare) firmware to migrate the 3MS to Happy Hare. It adds a ton of features and reliability improvements. However, it doesn't natively support this type of setup. The current 3MS software should work fine without a main printer extruder. When I complete migration to Happy Hare in a few months, this type of setup will become unsupported. I would recommend converting your setup to use one extruder as a main extruder, then feeding the other three into it as 3MS steppers.

I apologize for the inconvenience this may cause. I hope you aren't too far into your build, so this won't be too major of a modification.

kaiatkins, 2024-11-05:
I understand and happy to stay with current if that is ok. If I do see any sales for a direct drive and happen to get one I'll look at switching again. Thanks again for your work and communication during my build.

Closed 2024-11-20.

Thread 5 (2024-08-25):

[FR]: Endless spool

allenrowand, 2024-08-25:
### What feature do you want to see?

Was wondering if there was any plan to add endless spool, so that (for example) if T0 runs out of filament 3MS would pause, unload T0, load T1, and resume. I'm assuming the best way to implement that would be a runout sensor before each 3MS extruder…

Thanks!

3DCoded, 2024-08-26:
Experimental implementation is complete, and documentation is [here](https://3dcoded.github.io/3MS/experimental/endless/). Let me know if anything needs to be changed.

allenrowand, 2024-08-31:
Would like to talk to you about the project, can you email me at allen@west3d.com?

3DCoded, 2024-09-13:
I've implemented support for Endless Spool for another type of filament sensor setup: a single filament sensor setup, which is what my setup uses.

After some testing and evaluating the internal logic, a single filament sensor setup should be more reliable than a multi-filament sensor setup (the multi-filament sensor setup requires unloading the empty spool, which could lead to tip shaping issues, while the single filament sensor setup simply rams the new filament into the old without any unload required).

I've updated the documentation with the new recommendations and settings.

3DCoded, 2024-09-27:
Endless Spool is now implemented into the `main` branch.

Closed 2024-09-27.

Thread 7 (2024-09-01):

[FR]: Use of sensorless method to detect filament

yeorinhieut, 2024-09-01:
### What feature do you want to see?

Like ercf, we could use sensorless (tmc2209's feature to detect tolerance) method to check if filament is inserted into extruder. (by checking stop of filament)

Load -> check filament stopness -> extruder&3ms motor synchronization

We can then use 3ms with printers that doesn't have filament sensor on top of extruder!

Plus + Can I use skr pico to the 3ms?

3DCoded, 2024-09-03:
Currently, the 3MS doesn't support sensorless filament detection, but I plan on switching the 3MS's firmware to [Happy Hare](https://github.com/moggieuk/Happy-Hare) once support for it is added. Happy Hare firmware does support sensorless filament detection.

I've added experimental support for the SKR Pico.

3DCoded, 2024-11-11:
Hi @yeorinhieut, I just wanted to let you know that Happy Hare v3 Beta (which supports the 3MS and sensorless filament homing) is now available. See #29.

yeorinhieut, 2024-11-12:
Good news! Thanks for support!

Closed 2024-11-12.

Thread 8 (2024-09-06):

3MS Development Plan

3DCoded, 2024-09-06:
Here is the development plan for the 3MS project:

- [ ] TPU filament support [LINK](https://3dcoded.github.io/3MS/experimental/dualdrivetpu/)
- [ ] Expanding the no tip shaping feature using skinnydip string reduction
- [ ] 3MS Kits/Pre-assembled units

3DCoded, 2024-11-07:
> "3MS Kits/Pre-assembled systems" - that would be really great! Is this still planned for Q1/2025?

Yes. I'm planning this around February-March 2025.

> The BTT MMU has one disadvantage: limit of 4 colors. As far as I can see, only the A30T board supports more colors? How woild that work once 3MS has moved over to HappyHare?

There are two options in this case:

1. Use multiple BTT MMU boards. If you want to use multiple BTT MMU boards, you can open an issue and I will create a configuration to use multiple to get more colors.
2. I am converting over the existing configs to be compatible with Happy Hare. So far, only a few have been converted, but if you want to check on the progress, the configurations are [here](https://github.com/3DCoded/3MS/tree/main/happy-hare/configurations).

bsafh, 2024-11-07:
Sounds like multiple BTT MMU seem to be the better option, but perhaps I'll better wait for 3MS Kits:-)

ImChrono, 2024-11-08:
@3DCoded FYI, I'm tracking your migration development and adding the missing configurations to my repository. Once everything is ready for testing, it will be ready to merge.

3DCoded, 2024-11-08:
> @3DCoded FYI, I'm tracking your migration development and adding the missing configurations to my repository. Once everything is ready for testing, it will be ready to merge.

@ImChrono I think the only thing for you to migrate would be the Geetech A30 configuration. You can look at the [existing configurations](https://github.com/3DCoded/3MS/tree/main/happy-hare/configurations) to see how to create one. I think the SKR Mini or SKR Pico would be a good starting point.

Filament cutters are already natively supported by HH, so I think that should be an easier migration.

3DCoded, 2024-11-11:
Happy Hare beta v3 is released! See #29.

3DCoded, 2025-05-16:
@bsafh ,

3MS kits are now released! #56

https://west3d.com/products/3ms-the-simple-and-reliable-multi-material-system-kit-by-3dcoded

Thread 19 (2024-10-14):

[Bug]: Print Pauses after Prugeline

Mawe066, 2024-10-14:
### What happened?

Hey, the print pauses automaticly after the purge line. Maybe I am missing something in the slicer configuration but after 3MS starts and reads the T value, the print pauses and i have to manually resume it. Dont know if it is the same after another toolchange, havent done my testing so far.

### Klippy Log

[klippy.log](https://github.com/user-attachments/files/17363844/klippy.log)

3DCoded, 2024-10-14:
Does a prompt show up in Mainsail/Fluidd/KlipperScreen when this happens?

Mawe066, 2024-10-14:
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

The "Print is not paused, resume aborted" comes from an work around i have tried without succsess. Seems like it makes the purgeline, then checks again the filament sensor and pauses the print. The Start command is placed before the purge line, like the documentation said. I am using orca slicer. Except for the two thing to add in the maschine gcode, there is nothing more that needs modifications?

3DCoded, 2024-10-14:
Did the print just skip from starting to ending without actually printing anything?

Mawe066, 2024-10-14:
No, I printed flow calibration in a single color.

Right at the beginning or after the purge line? Didn't see the need of an clear pause before it actually paused

3DCoded, 2024-10-14:
Generally, adding a `CLEAR_PAUSE` before even your heating/homing commands is a good practice for a Klipper start G-code (with or without the 3MS). The `CLEAR_PAUSE` command resets Klipper's internal pause state.

When the 3MS loads filament, do you hear a clicking noise? Does the filament actually get loaded to your filament sensor?

Mawe066, 2024-10-14:
The filament is loaded. Like I said, it makes the purge line and then right into the pause state

3DCoded, 2024-10-14:
This sounds like your 3MS's `fsensor_delay` setting needs to be increased. Can you try increasing your `fsensor_delay` to something large, like 10,000ms?
```
SET_MMMS_SETTINGS FSENSOR_DELAY=10000
```

If that works, slowly decrease your `fsensor_delay` to be as low as possible while still not pausing the print automatically.

To save permanently, edit your `3ms/settings.cfg`:
```
[gcode_macro MMMS_SETTINGS]
other settings...
fsensor_delay: 10000
```

Mawe066, 2024-10-14:
I set the delay to 10.000 and it still pauses after the purgeline. I eben tried to increse the settings in my filament sensor itself. Still no changes. i have an BTT SFS 2.0.

Mawe066, 2024-10-15:
Another thing, not bug related.  Is it possible to pre load the initial extruder before loading via 3ms? My specific setup reqiuries this :D

Mawe066, 2024-10-15:
Hey, i have another question i cant find anything about in the documentation. In orca slicer i have set an cooling tube position to 35mm and filament park position to 160 what is in between my sensor and my direct drive extruder. Is 3ms ment to load to the parking psoition and let orca/super slicer handle the rest? If yes, i need another 160 millimeters to load with my initial tool. If i ignore my parking position, and load directly into the nozzle, i have an massive blob. For now i cant figure out how the set the values right in my slicer and my loading and unloading distances

ImChrono, 2024-10-15:
Just for reference, I also use Orca Slicer. I've set the cooling tube position and length to 0, allowing the 3ms macros to handle the task. My setup is slightly different, as I've positioned the filament sensor after the extruder gears. However, I don’t think this makes a significant difference, as long as the values are correctly configured in the macro settings.

Mawe066, 2024-10-15:
I have 4 extruders that lead through the sensor to the extruder that's directly attached to the hot end. But how does the tip shaping works without the slicer settings?

ImChrono, 2024-10-15:
I'm sorry, but I can't help with that aspect. I've completely bypassed filament tip shaping. Initially, I only printed with PLA, and now I've added a filament cutter, which I’ve been using reliably ever since.

3DCoded, 2024-10-15:
> I have 4 extruders that lead through the sensor to the extruder that's directly attached to the hot end. But how does the tip shaping works without the slicer settings?

You need slicer settings for tip shaping. The [Materials table](https://3dcoded.github.io/3MS/guides/materials/) can show you which filaments need tip shaping, some recommended tip shaping settings, and if they support [No tip shaping](https://3dcoded.github.io/3MS/guides/notip/). I am also currently working on a faster tip shaping method.

3DCoded, 2024-10-15:
> Hey, i have another question i cant find anything about in the documentation. In orca slicer i have set an cooling tube position to 35mm and filament park position to 160 what is in between my sensor and my direct drive extruder. Is 3ms ment to load to the parking psoition and let orca/super slicer handle the rest? If yes, i need another 160 millimeters to load with my initial tool. If i ignore my parking position, and load directly into the nozzle, i have an massive blob. For now i cant figure out how the set the values right in my slicer and my loading and unloading distances

Yes. The 3MS is meant to load the the parking position and let the slicer handle the rest. The slicer should automatically handle the extra loading. Usually, you only need to set the 3MS's `load_distance` to 5-15mm more than your `unload_distance`. To fix the blob, you can set your slicer's `Printer settings` -> `Multimaterial` -> `Extra loading distance` to a negative number, like `-20`.

Mawe066, 2024-10-15:
But when I load it to the parking position in the initial loading, then there is 160mm missing in my case. Is there a possibility to implement a macro or something else like that into the initial loading process?

3DCoded, 2024-10-15:
The proper sequence of events for a tool change is:
- Slicer performs tip shaping
- Slicer unloads to parking position
- 3MS unloads from parking position
- 3MS loads to parking position
- Slicer loads from parking position
- Slicer performs purging

Does your tool change follow this sequence?

Also, I have a few more questions:
- What did you set the `Extra loading distance` setting to?
- What slicer are you using?
- What are your 3MS `unload_distance` and `load_distance` settings?

Also, for the earlier problem with the filament motion sensor, you can add these lines before and after your `MMMS_START` call in your Start G-Code:
```
SET_FILAMENT_SENSOR SENSOR=encoder_sensor ENABLE=0
MMMS_START
SET_FILAMENT_SENSOR SENSOR=encoder_sensor ENABLE=1
```
This will disable your filament motion sensor during `MMMS_START`, then re-enable it after.

Mawe066, 2024-10-15:
My Question is specifically for the first load, not a color change. How does it handle the, in my case, missing 160mm filament from the parking position to the tip of the nozzle, since there is no tip shaping and unloading required. I understand how the color change works, but that's not my question.

Mawe066, 2024-10-16:
I think you can close this thread now. I have found an solution for my specific build related problem. I just added the missing 160mm of filament after the loading sequence in the start code. Works like a charm now.

Closed 2024-10-16.

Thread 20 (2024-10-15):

Manual filament cutter

ImChrono, 2024-10-15:
### What feature do you want to see?

Hi there,
I'm opening this feature request to track and provide suggestions for a manual filament cutter feature. I've already made some local modifications to the project, and it's working great.

What I've done is create a new extruder for bed slinger-type 3D printers, incorporating a blade and a specific filament cutter position. Before I commit my work, I wanted to explore ways to further improve the workflow and, more importantly, assess whether such a feature is truly needed.

I've set up a parking position near the filament cutter, and during each filament change, I move the toolhead to this position and activate a custom macro. This macro executes four quick movements to trigger the filament cutter, allowing the filament to be changed as usual.

What I'd like to add is a custom retraction to save filament and, if possible, make the filament "poop" out instead of relying on the purge tower. I'll also share some photos of the setup and process for reference.

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

https://github.com/user-attachments/assets/3de968df-6425-4234-8b5b-bedcf8b73a23

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

3DCoded, 2024-10-15:
I've experimented with filament cutters in the past, and have had a hard time finding a good design for my printer (Prusa MK3S+), so I haven't been able to do much testing.

From my limited testing with filament cutters, I've come up with some pro's and con's.
**Pros:**
- Faster
- More reliable
- No need for tip tuning

**Cons:**
- Need printer-specific hardware
- Extra waste is generated

I'm also working on a faster/simpler tip shaping algorithm that should also make tip shaping much easier to tune.

With that said, if you have a working setup, I'm open to pull requests. If you do a PR, to keep the 3MS software modular, please put the filament cutter configuration in either its own config file (e.g. `cutter.cfg`) or its own folder with multiple files inside (e.g. `cutter/settings.cfg` and `cutter/macros.cfg`).

I am planning on migrating to [Happy Hare](https://github.com/moggieuk/Happy-Hare) firmware as soon as support for 3MS-style systems is added, which does support filament cutters (and much more). I'd recommend looking at its source code for the extra retraction before cutting, and custom purge locations.

ImChrono, 2024-10-16:
Thank you for this awesome project!
As you mentioned, filament cutting is more reliable and faster. While I’m not a fan of waste either, for now, it’s the only dependable solution that works with stringy filaments and multi-material setups. That said, I'm working on rebasing the macros and making them modular, so I can commit the changes to the main branch. I still need to figure out how to make the MMMS_UNLOAD macro read and use the new module only if it’s actually enabled—once that’s done, I'll commit a first version.

The next step would be to add filament retraction.

Off-topic: Happy Hare is a very cool project! But the last time I checked, the 3MS-style configuration was still theoretical. In my opinion, using multiple motors with multiple extruders is more cost-effective than building an MMU. Older printers like the Ender 3 are cheaper nowadays and can serve as a great starting point for making a 3MS-style setup with minimal additional accessories.

3DCoded, 2024-10-16:
To check if a module exists, you can check if one of its macros exists. For example, if one of your macros is named `CUT_FILAMENT`, you could use:

```
{% if "gcode_macro CUT_FILAMENT" in printer %}
; Filament cutting is enabled
{% else %}
; Filament cutting is disabled
{% endif %}
```

I asked the developer of Happy Hare about 3MS-style systems ([#371](https://github.com/moggieuk/Happy-Hare/issues/371)), and they said that the functionality was implemented, but the configuration isn't exposed. I looked through the Happy Hare code, and I'm pretty sure the `development` branch has that code. I'm currently waiting for it to be more tested and documented before moving the 3MS over to Happy Hare.

3DCoded, 2024-10-16:
For filament retraction, you can probably edit the `Toolchange` macro and add a retract command at the start, using the same method I recommended earlier:
```
{% if "gcode_macro "RETRACT_BEFORE_CUT" in printer %}
; Filament cutting is enabled
RETRACT_BEFORE_CUT
{% endif %}
```

Because there are many different filament cutter designs available, I would recommend making the settings configurable, like the `MMMS_SETTINGS` macros in `3ms/settings.cfg`.

ImChrono, 2024-10-16:
I've just committed the first revision to my own repository. This configuration includes a decompress pin on the X-axis. Before merging and submitting a PR, I’ll complete the "manual mode" filament cutter so it can be configured for both the X and Y axes, making it compatible with CoreXY systems as well. I’m aware that servo mode is an option, and I plan to work on that too. I still need to update a few files, and once I'm done, I'll update you.

3DCoded, 2024-10-16:
Your implementation looks good! I'd recommend a couple things in its current state:
- Implementing `SET_CUTTER_SETTINGS` and `GET_CUTTER_SETTINGS` macros for easier settings changes
- Making the number of cut repetitions configurable

ImChrono, 2024-10-16:
I've added setters and getters and parameterized the cut retries. I'm currently testing it with a long print, and I’ll check the results tomorrow.

3DCoded, 2024-10-16:
The setters/getters look good. Thank you for using the same code conventions as the rest of the 3MS code.

On a side note, could you please post the link to that Y-splitter?

ImChrono, 2024-10-17:
You’ll need 5 PC4-M10 connectors. Be careful not to push the Bowden tubes too far into the four inputs, as this can block the filament path. The model itself already includes a support structure. I recommend printing the main model in ABS or PETG, and the support pin in a different material to make removal easier.

Please note, I’ll be publishing a newer version of the model soon that addresses some issues I encountered during printing.
[4-Way Y-Splitter Model](https://www.printables.com/model/1042279-4-way-y-splitter)

3DCoded, 2024-10-17:
Thank you! I've been trying to find a good 4-way splitter. I'll print that out soon. How did the test print go?

ImChrono, 2024-10-17:
Still printing, looks good for now.
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

ImChrono, 2024-10-18:
Unfortunately, the print failed due to issues with the Automatic Pause. I wasn't home, and the printer timed out.

The good news is that the cutting macros are working great!

Off-topic:
I’m still investigating the cause of the pause issue. I’m not sure if it’s related to timing (I’ve tested up to 10 seconds). I’ve also noticed that my Raspberry Pi occasionally detects undervoltage, so it could be a system-related issue.
However, I bypassed the problem by editing the settings as follows:

[filament_switch_sensor hsensor]
pause_on_runout: False
switch_pin: EBBCan:PB6

Keep in mind that I have two endstops. The one I'm using for the 3MS macros is positioned after the extruder gears and is not being used as a filament runout sensor, so automatic pause isn’t a feature I need.

3DCoded, 2024-10-18:
The automatic pause should only happen if the filament sensor shows that the color swap failed. If this keeps happening, let me know with a klippy.log, and I can diagnose the problem.

ImChrono, 2024-10-18:
I've attached the klippy.log. I hope you can find the culprit.
[klippy.zip](https://github.com/user-attachments/files/17440473/klippy.zip)

3DCoded, 2024-10-18:
If you can catch this happening, I have a few main ideas:

1. If the `klippy.log` indicates that your `fsensor` (not `hsensor`) was triggered, disable the `fsensor` during a print and test again
2. If the `klippy.log` indicates that your `hsensor` was triggered, increase your 3MS `fsensor_delay` setting and test again
3. If the color swap actually failed (e.g. the previous filament failed to unload or the next filament failed to load), the automatic pause was expected behavior. Either your LCD or Mainsail/Fluidd/KS should display a message in this case.

This `klippy.log` indicates point two, so I'd recommend increasing your `fsensor_delay` setting. If this happens again, look back over the three points and follow the suggested solution.

ImChrono, 2024-10-18:
What I don't understand is that the majority of filament swaps work perfectly, but occasionally the hsensor got triggered (or at least, I assume that's what's happened). The fsensor is fine—I’ve tried printing with the sensor disabled, and the issue still occurred.

Another thing to note: I’m currently printing with the setting hsensor: pause_on_runout: False and fsensor disabled, and no issues have occurred so far. However, it could just be a placebo effect, as I restarted the firmware before this test.

ImChrono, 2024-10-19:
This time, the print was successful!

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

ImChrono, 2024-10-22:
Another successful print! This is the first print with filament retraction enabled. I still need to fix a few issues, and then I'll commit the first revision.

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

3DCoded, 2024-10-22:
Those prints look great! I'm looking forward to your PR.

3DCoded, 2024-10-31:
Closing as the PR is merged.

Closed 2024-10-31.

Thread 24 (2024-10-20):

Filament feeder splitter

ImChrono, 2024-10-20:
I'm opening this thread to track and discuss filament splitter for the toolhead. Below is the link to my latest revision:

https://www.printables.com/model/1042279-no-catch-4-way-y-splitter-pc4-m10

This updated revision is designed for easier installation and printing. No supports are needed—just follow the slicer configuration provided.

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

Improvements and alternatives are welcome

3DCoded, 2024-10-20:
Thank you for designing this. I've been using the original version on my setup for a few days now and have had no problems so far. Utilizing the `Bridge counterbore holes` setting is a good way to remove supports on prints.

ImChrono, 2024-10-20:
Good to hear it's working well for you too. This new revision is designed to be more forgiving when installing the Bowden tubes, ensuring they’re aligned at the same distance. It also helps reduce unwanted pressure that can occur if the feeder motor isn't properly aligned with the extruder motor.

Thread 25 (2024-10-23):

Rapid Tip Shaping Algorithm - Feedback Welcome

3DCoded, 2024-10-23:
## Introduction

> [!NOTE]
> With the migration to Happy Hare firmware, this feature will become obsolete.

For the past couple of weeks, I have been working on a new method of performing tip shaping. Instead of running in the slicer, this method runs as a Klipper macro. This allows for quickly trying out new settings to see what works best for each of your filaments.

Before I explain more, I want to give credit where credit is due. The idea for tip shaping in a macro came from [Happy Hare Firmware](https://github.com/moggieuk/Happy-Hare). The basis for this algorithm was originally from [this post](https://www.3dchameleon.com/forum/your-3d-chameleon-creations/20-second-color-changes-on-k1-max) in the 3DChameleon forum.

So...how is it better than standard tip shaping?

- **Faster:** In my testing, this method is around 1.5-2.5x faster than standard tip shaping, resulting in ~20s color swaps
- **Easier Tuning:** As I mentioned earlier, this method allows for testing your tip shaping with a simple macro
- **More Reliable:** In my testing, this method has proved **significantly** more reliable than standard tip shaping. This is likely because tuning tips with traditional tip shaping is a long process, so I settled for decent tips, not near-perfect ones. With this method, I kept tuning until my tips looked nearly perfect.

## Filament Cutters

Before we go further, if you can install a mechanical filament cutter on your printer below your filament sensor (closer to the nozzle), please do that! Filament cutters are much, **much** faster and more reliable than tip shaping will ever be, and there's no tuning required.

Thank you @ImChrono for implementing this! The documentation is available [here](https://3dcoded.github.io/3MS/guides/manualcutter/).

## How it Works

If you aren't using a filament cutter, back to tip shaping. This algorithm uses only **four** G-Code moves. That means that while there are less things to tune, each setting can have a big impact on your filament tips.

I've broken them down below:

1. Quickly push the filament out of the nozzle
    - This is essentially the ramming stage of standard tip shaping
    - This part actually forms the tip of the filament
    - This leaves a string of filament on the nozzle that is meant to be "caught" by the wipe tower (explained more later)
2. Quickly retract the filament to the cooling tube
    - Tuning this speed is **crucial** to keeping the filament tip shape through the next step
3. Slowly retract the filament through the cooling tube
    - This is similar to the cooling moves performed by standard tip shaping, however it doesn't move the filament back and forth
    - This step controls how flat/sharp/stringy the filament tip is
    - This also controls how molten the filament tip is when it exits the extruder
4. Quickly retract the filament out of the extruder
    - This step isn't too important to tune if the previous three steps were done right

## Documentation

Documentation for rapid tip shaping is available [here](https://3dcoded.github.io/3MS/experimental/rapidtip/).

TODO's for rapid tip shaping:

- [ ] IN PROGRESS: Support for custom `PARK` and `UNPARK` macros
- [ ] Any feedback given here

TODO's for the documentation:

- [x] Slicer setup
- [ ] Pictures of filament tips
- [ ] Any feedback given here

## Feedback

Please feel free to give any feedback on this feature. This is still in development, so expect frequent changes.

bsafh, 2024-11-07:
"Thank you @ImChrono for implementing this! The documentation is available [here](https://3dcoded.github.io/3MS/guides/manualcutter/)."

Which cutter can be used and how to connect it to the controller ???

3DCoded, 2024-11-07:
Any filament cutter that cuts below the filament sensor can be used. It is controlled by a mechanical switch that the printhead pushes against the frame/gantry of the printer to cut the filament.

bsafh, 2024-11-07:
Ok ... limit still a bit lost how to find one, but well ...

3DCoded, 2024-11-07:
What printer are you using? There are a some pre-designed filament cutters for certains printers (e.g. Filametrix cutter for Voron printers)

bsafh, 2024-11-07:
for this direct drive extruder: https://www.tronxy3d.com/de/products/tronxy-3d-printer-parts-high-temperature-print-head-for-x5sa-series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 (320°C version) and this Klipper control unit https://www.tronxy3d.com/products/tronxy-klipper-firmware-upgrade-kits?variant=44680278671604 - it's a Tronxy 5XSA Pro printer

bsafh, 2024-11-07:
Two printer, but only one with Klipper ...

1) Geeetech A30 (not Klipper)

2) Tronxy X5SA Pro, but with the Klipper Update Kit and an direct drive
extruder/hotend update kit:

for this direct drive extruder:
https://www.tronxy3d.com/de/products/tronxy-3d-printer-parts-high-temperature-print-head-for-x5sa-series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
(320°C
version) and this Klipper control unit
https://www.tronxy3d.com/products/tronxy-klipper-firmware-upgrade-kits?variant=44680278671604
-
it's a Tronxy 5XSA Pro printer

Regards

Christian B.

Christopher Mattar ***@***.***> schrieb am Do., 7. Nov. 2024,
22:41:

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

ImChrono, 2024-11-08:
I also suggest opening a new issue so that this thread can stay focused on tip shaping suggestions and improvements

bsafh, 2024-11-08:
> I also suggest opening a new issue so that this thread can stay focused on tip shaping suggestions and improvements

https://github.com/3DCoded/3MS/issues/27#issue-2644777164

3DCoded, 2024-11-08:
> As a side note, I'm planning to release a second PR soon, which will include filament retraction between swaps to save filament, as well as support for a servo cutter.

Before you spend too much time working your PR, the beta of Happy Hare v3 (which supports the 3MS) should be released very soon. All the existing 3MS macros will be archived after the final release of Happy Hare, including contributed code.

ImChrono, 2024-11-08:
That's great news! As you pointed out, Happy Hare is a solid alternative. Once TYPE B MMU gains full compatibility, I'll switch my new setup to that firmware as well.

bsafh, 2024-11-08:
🙂🙃

I'll see. Still new to Klipper...

3DCoded, 2024-11-08:
> 🙂🙃
>
> I'll see. Still new to Klipper...

[This](https://klipper.discourse.group/t/macro-creation-tutorial/30) is a really good guide for writing Klipper macros.

3DCoded, 2024-12-10:
Closing as the 3MS is now fully migrated to HH

Closed 2024-12-10.

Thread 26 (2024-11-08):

[FR]: filament cutter (servo driven)

bsafh, 2024-11-08:
I also have a Tronxy X5SA (not Pro) but modified the gantry with a custom setup using linear motion instead of rollers. Unfortunately, I don’t have the same print head, so I can’t help with designing a custom mechanical cutter. However, you could try remixing this model:
[Small Filament Cutter](https://www.printables.com/model/793488-small-filament-cutter/files).

I think there should be enough space to place the cutter between the extruder and the hotend

As a side note, I'm planning to release a second PR soon, which will include filament retraction between swaps to save filament, as well as support for a servo cutter.

I think a servo cutter might be an easier option for your printer since it would minimize the need to move the printhead, which looks a bit heavy...

_Originally posted by @ImChrono in https://github.com/3DCoded/3MS/issues/25#issuecomment-2464252630_

bsafh, 2024-11-08:
sorry, duplicate

3DCoded, 2024-11-08:
I'll close this duplicate.

Closed 2024-11-08.

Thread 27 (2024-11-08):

[FR]: filament cutter (servo driven)

bsafh, 2024-11-08:
### What feature do you want to see?

Which cutter can be used ?

To be more precise: for this direct drive extruder:

Tronxy X5SA Pro, but with the Klipper Update Kit and an direct drive
extruder/hotend update kit:

for this direct drive extruder:
https://www.tronxy3d.com/de/products/tronxy-3d-printer-parts-high-temperature-print-head-for-x5sa-series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
(320°C version) and this Klipper control unit
https://www.tronxy3d.com/products/tronxy-klipper-firmware-upgrade-kits?variant=44680278671604

It's very tight (direct drive - not much space between extruder an hotend by design ...) and quite heavy

bsafh, 2024-11-08:
_Originally posted by @ImChrono in https://github.com/3DCoded/3MS/issues/25#issuecomment-2464252630_

I also have a Tronxy X5SA (not Pro) but modified the gantry with a custom setup using linear motion instead of rollers. Unfortunately, I don’t have the same print head, so I can’t help with designing a custom mechanical cutter. However, you could try remixing this model:
[Small Filament Cutter](https://www.printables.com/model/793488-small-filament-cutter/files).

I think there should be enough space to place the cutter between the extruder and the hotend

As a side note, I'm planning to release a second PR soon, which will include filament retraction between swaps to save filament, as well as support for a servo cutter.

I think a servo cutter might be an easier option for your printer since it would minimize the need to move the printhead, which looks a bit heavy...

_Originally posted by @ImChrono in https://github.com/3DCoded/3MS/issues/25#issuecomment-2464252630_

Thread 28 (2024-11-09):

[Bug]: Klipper pressure_,advance stops working after 3MS install

deemax-real, 2024-11-09:
### What happened?

Hi, after 3MS install Klipper pressure advance have mo impact on the print. Pressure advance and smooth time windows disappeared from mainsail gui and even gcode pressure advance have no impact on print (round corners). Also extruder acceleration from printer.cfg stops working (now extruder works with same ACC as axes). Can provide logs before and after 3MS installation if needed.

### Klippy Log

Z

deemax-real, 2024-11-09:
[config-20241109-174017.zip](https://github.com/user-attachments/files/17688828/config-20241109-174017.zip)
[klippy.log](https://github.com/user-attachments/files/17688829/klippy.log)

3ms controller steppers.cfg are for Ender 4.2.2 motherobard under btt_skr_mini_e3_v2

3DCoded, 2024-11-09:
I can't see anything wrong with your config. Can you try a PA calibration print?

deemax-real, 2024-11-09:
Printer seems to ignore pressure advance setting and even command from console during printing. Can send photo of model printed with pa working and some model from today wit obvious overextruded corners. Even silly high pa value not change anything :)

3DCoded, 2024-11-09:
Does the issue still occur if you comment out this line in your `printer.cfg`:

```
[include 3ms/main.cfg]
```

and add a test Dynamic Macro as explained [here](https://3dcoded.github.io/DynamicMacros/setup/#configuration)?

deemax-real, 2024-11-09:
PA and Smooth time coming back after commenting 3ms/main.cfg

but....
Dynamic Macros test done nothing. No response for MYTEST :/
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

deemax-real, 2024-11-09:
After some tests I've find dynamic macros test didn't work with m117 command :/
After change in dynamic.cfg I'm getting response in console.
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

3DCoded, 2024-11-09:
This is really confusing. Can you try the following steps and see if PA works?

1. Uncomment the `[include 3ms/main.cfg]` line in your `printer.cfg`
2. In `3ms/main.cfg`, comment out the `[dynamicmacros 3ms]` section.

Also, I would recommend replacing your main `[mcu]` configuration with a `/dev/serial/by-id` path (it's currently `/dev/ttyAMA0`), so it doesn't get confused with the 3MS board.

deemax-real, 2024-11-09:
After uncommenting 3ms/main.cfg PA gone from gui

Pi connected by serial with printer mb so can't change to usb connection. Pi seen both mcu's without any problem and everything works (3ms motor spins and sync with main extruder motor) so don't think connection is a problem but later today or tomorrow I can try back to us connection for both mcu's.

3DCoded, 2024-11-09:
> 2. In 3ms/main.cfg, comment out the [dynamicmacros 3ms] section.

Did you try this?

deemax-real, 2024-11-09:
Yes. No change

3DCoded, 2024-11-09:
Ok. That helps to narrow down the issue. I'm guessing it has to do with how the `steppers.cfg` file is set up (probably my fault). I'll have to check this.

deemax-real, 2024-11-09:
Happy to try any solution :)

3DCoded, 2024-11-09:
Hmm... That was the first configuration I used with the 3MS. I think it has to do with the serial port. I would recommend converting your serial to use `/dev/serial/by-id` for both the 3MS and your main MCU.

deemax-real, 2024-11-09:
Trying do this now but can't get 2 usb IDs from terminal. Don't know why.

deemax-real, 2024-11-09:
Usb sorted.
Both mcu's connected by usb to pi
All changes/comments reverted.
No PA and Smooth time :(

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

3DCoded, 2024-11-09:
I think we're going to have to go through `3ms/main.cfg` and figure out what is causing the error. So far, it seems like the `steppers.cfg` is the issue. What happens if you comment out the `[include ./controllers/.../steppers.cfg]` line in `3ms/main.cfg`?

Thank you for your patience as we work through this error!

deemax-real, 2024-11-09:
After commenting steppers.cfg PA comes back.
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

I'm happy to help (and desperate to find a solution) as I want my ender printing in colours for my sons :)

3DCoded, 2024-11-09:
That helps to narrow down the issue. I have an idea:

In the `3ms/controllers/skr_mini_e3_v2/steppers.cfg`, can you comment out all the `extruder_stepper` sections?

If that doesn't work, can you try also commenting out the `[mcu 3ms]` section?

Let me know if either of those work (the 3MS won't work in this case but it should at least give another pointer to find the root cause).

deemax-real, 2024-11-09:
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

3DCoded, 2024-11-11:
Aside from updating Klipper, I don't really have other ideas. `extruder_stepper`s are part of standard Klipper, so I expected them to "just work" with any Klipper setup. If you can remove the 3MS configuration and add an `extruder_stepper` configuration, and PA still disappears, you might be able to get some help from the [Klipper Discourse](https://klipper.discourse.group/).

Alternatively, Happy Hare v3 beta just got released, which now supports the 3MS. It uses an entirely different configuration system, so if you want to become a beta tester, see #29.

deemax-real, 2024-11-11:
Hi, great news about Happy Hare beta. I'll lean into this way and we'll see if  PA working.
Happy to be a beta tester.

3DCoded, 2024-11-15:
Closing this issue as it's been moved to the HH Discord.

Closed 2024-11-15.

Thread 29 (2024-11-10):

Happy Hare v3 Beta! 🎉

3DCoded, 2024-11-10:
🐰 🐰🐰 Happy Hare v3.0 for 3MS 🐰 🐰🐰

**Happy Hare v3.0 beta** has just been released and now supports the 3MS MMU.. 🎉

Firstly, thank you to:
- @moggieuk for developing Happy Hare, adding support for the 3MS, and helping work through testing.
- @chadakenn for testing HH and designing a work-in-progress 3MS enclosure box: https://www.printables.com/model/1067703-wip-3ms-mmu-using-btt-mmb
- @ImChrono for contributing filament cutter functionality to the original 3MS, helping with testing HH, and designing this 4-way Y splitter: https://www.printables.com/model/1042279-no-catch-4-way-y-splitter-pc4-m10

**What is Happy Hare?**
- For those that are not aware, Happy Hare is the Klipper extension to manage all MMUs / Automated Filament Changers.  Until recently it only supported "selector" based designs (ERCF, Tradrack) but that has now been extended to fully support mutli-stepper designs, like the 3MS.
- Happy Hare manages all aspects of filament loading/unloading/changing but also very detailed control of:
   - Extruder loading, priming and purging, **toolhead sensor** option.
   - Movement and parking control for filament cutting options
   - Full **Spoolman** integration (rfid/QR tracking)
   - Variable stepper synchronization control: Belay, or another proportional sync feedback system
   - Full control **Blobifier** as alternative to the wipe-tower
- Has customized **[KlipperScreen extension](https://github.com/moggieuk/KlipperScreen-Happy-Hare-Edition)** for easy MMU control
- Lots more!

**How to get started**
- Review the [quick start guide](https://github.com/moggieuk/Happy-Hare/wiki/Quick-Start-3MS) (as well as the rest of the documentation)
- Join the dedicated 3MS / Happy Hare [Discord Channel](https://discord.com/channels/1305204275315474452/1305204466374672474)
- Ask questions (here and on the Happy Hare discord)
- Just remember this is BETA and thus you must elect to install from the **"v3beta"** branch of Happy Hare

Closed 2024-12-09.

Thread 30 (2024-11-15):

[MCU]: Fly-D7

kintarojs, 2024-11-15:
### What kind of controller is this?

extra MCU (MCU used specifically for the 3MS)

### Controller name

Fly-D7

### More information

https://mellow.klipper.cn/en/docs/category/fly-d7

3DCoded, 2024-11-15:
Hi @kintarojs,

Thank you for your controller request. I have added support for the Mellow Fly D7 board in the existing 3MS firmware and in Happy Hare. Documentation will be available soon.

3DCoded, 2024-11-16:
Sorry for the errors. Thank you for your fixed version. I'll update this.

3DCoded, 2024-11-16:
I've fixed as suggested, and the documentation is now available [here](https://3dcoded.github.io/3MS/setup/controllers/mellowflyd7/). Let me know if there's anything I need to change.

Closed 2024-11-29.

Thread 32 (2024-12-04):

[DOCS]: Supplement the documentation on BTT MMB

Jager-f, 2024-12-04:
### What kind of documentation issue is this?

- [ ] Typo
- [ ] Incorrect information
- [ ] Unclear information
- [X] Missing information
- [ ] Contradictory information

### How do you think the documentation should be improved?

In the current version of the document, when power is supplied to the HVIN, the board will not be powered and will not start. It is mandatory to install the jumper VUSB, to power the processor from USB.

3DCoded, 2024-12-04:
Hi @Jager-f ,

Thank you for finding this issue in the documentation. I have updated the beta documentation [here](https://3dcoded.github.io/3MS-docs/setup/controllers/bttmmb/). When Happy Hare v3 gets fully released, this will replace the current documentation.

Jager-f, 2024-12-08:
These two lines need to be swapped. The LED will light up only after connecting the USB

If the MMB lights up, you wired it correctly!

Finally, plug the MMB into your Klipper host with the cable that came with it.

3DCoded, 2024-12-09:
Hi @Jager-f ,

I have switched the last two lines in the **main** documentation (the beta docs are now fully migrated to the main docs).

Jager-f, 2024-12-09:
I made a compact and lightweight Y-splitter, with tubes fastened with 1 screw for 3MS) https://www.printables.com/model/1092036-4-tube-y-splitter-for-mmu

3DCoded, 2024-12-09:
> I made a compact and lightweight Y-splitter, with tubes fastened with 1 screw for 3MS) https://www.printables.com/model/1092036-4-tube-y-splitter-for-mmu

That's an interesting design. This is good timing too, as I'm trying to figure out the easiest to print and most reliable Y-spliters. I may look into this as I already have the required hardware.

3DCoded, 2024-12-09:
Also, @Jager-f ,

If you want more people to test out your Y-splitter, you can post the link on the 3MS discord and the 3MS channel at the HH discord. Both links are in the homepage of the docs.

Closed 2024-12-04.

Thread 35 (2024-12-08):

[MCU]: BTT Kraken V1.0

t7git, 2024-12-08:
### What kind of controller is this?

main MCU (using spare stepper ports on existing MCU)

### Controller name

BTT Kraken V1.0

### More information

This is gutting out an old Neptune 4 Max only using the hotend/extruder and obviously the bones from the Neptune 4 Max) I use my old laptop it's an Intel i5 processor for my Klipper host. Then I use a BTT Kraken as my main board. (60V on the stepper motors, 24V on the Bed Power, 24V on the MCU power) The stepper motors are X, Y, (corrupted not used), 3MS0, Z1, Z, 3MS1, E

Then on a secondary MCU it's the BTT Manta M8P and I have two 2209 stepper motor drivers installed (I own five 2209 but haven't purchased more extruders yet (I only have 4 right now)). The two separate 2209 on the Manta M8P are 3MS3 and 3MS2.

The Manta's type C connection doesn't work properly so I use the UART to connect the Manta to the Klipper host. I also use a CAN to USB adapter and own the EBB42 that is coming in the mail today that is replacing a broken one.. (BTT's quality control is crazy.. never returned so many things in my life) The Manta using UART is using a Serial to USB adapter. The new EBB42 is going to replace the extruder, hotend thermistor, filament run out sensor, inductive probe, servo, and hotend heater.

3DCoded, 2024-12-09:
Hi @t7git ,

Just to confirm the steppers:

- `3ms0` is `S4`
- `3ms1` is `S7`
- `3ms2` is Manta `X`
- `3ms3` is Manta `Y`

I'm going to merge #36 into this to make it easier to keep track of these.

3DCoded, 2024-12-10:
Hi @t7git ,

I have added the configuration. It is available [here](https://github.com/3DCoded/3MS/tree/custom-configs/configs/35) .

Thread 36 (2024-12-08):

[MCU]: BTT Manta M8P V2.0

t7git, 2024-12-08:
### What kind of controller is this?

extra MCU (MCU used specifically for the 3MS)

### Controller name

BTT Manta M8P V2.0

### More information

This is gutting out an old Neptune 4 Max only using the hotend/extruder and obviously the bones from the Neptune 4 Max) I use my old laptop it's an Intel i5 processor for my Klipper host. Then I use a BTT Kraken as my main board. (60V on the stepper motors, 24V on the Bed Power, 24V on the MCU power) The stepper motors are X, Y, (corrupted not used), 3MS0, Z1, Z, 3MS1, E

Then on a secondary MCU it's the BTT Manta M8P and I have two 2209 stepper motor drivers installed (I own five 2209 but haven't purchased more extruders yet (I only have 4 right now)). The two separate 2209 on the Manta M8P are 3MS3 and 3MS2.

The Manta's type C connection doesn't work properly so I use the UART to connect the Manta to the Klipper host. I also use a CAN to USB adapter and own the EBB42 that is coming in the mail today that is replacing a broken one.. (BTT's quality control is crazy.. never returned so many things in my life) The Manta using UART is using a Serial to USB adapter. The new EBB42 is going to replace the extruder, hotend thermistor, filament run out sensor, inductive probe, servo, and hotend heater.

I just copied & pasted it but the BTT Manta M8P V2.0

It could technically be used as the main board but I have it as a secondary right now. Planning on using eight extruders someday for more color options :)

3DCoded, 2024-12-09:
Merged into #35.

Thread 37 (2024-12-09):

Migration to Happy Hare v3

3DCoded, 2024-12-09:
With the final release of Happy Hare v3.0, the 3MS will now entirely migrate to Happy Hare firmware. The old docs and software will be saved in the `legacy` and `docs-legacy` branches, but it his **highly** recommended to switch to Happy Hare firmware. If you already used the Happy Hare beta, all you need to do is:

```
cd ~/Happy-Hare
./install.sh -b main
```

If this is a new installation, follow [this guide](https://github.com/moggieuk/Happy-Hare/wiki/Quick-Start-3MS) .

Also, please join the 3MS channel in the Happy Hare Discord:

https://discord.gg/8nTTEZeuvb

and the 3MS Discord:

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

brentdeacon23, 2024-12-10:
I am able to clone the HH repo but I cant run install.sh, im assuming this is due to the K1's "klipper" version. Any insight?

3DCoded, 2024-12-10:
> I am able to clone the HH repo but I cant run install.sh, im assuming this is due to the K1's "klipper" version. Any insight?

Hi @brentdeacon23 ,

Someone on the #3ms channel in the HH Discord was able to setup HH on a K1. From what I can tell, the two main things that they did that fixed it was:

1. Install bash
2. Install python3 with:

    ```
    opkg install python3
    ```

Closed 2024-12-18.

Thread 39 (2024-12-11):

[Bug]: Unknown Pin Chip Name '3ms'

brentdeacon23, 2024-12-11:
### What happened?

I am on the SKR Mini V2. the line in mmu.cfg in the specific file for that board, the line [static_digital_output usb_pullup_enable]
pins: !3ms: PA14 thows an Unknown pin chip name '3ms' on the k1

### Klippy Log

[klippy.log](https://github.com/user-attachments/files/18087769/klippy.log)

3DCoded, 2024-12-11:
Hi @brentdeacon23 ,

Thank you for finding this bug. I have updated the `mmu.cfg` for the SKR Mini with a fix. After re-installing the file, the error should no longer be present.

brentdeacon23, 2024-12-11:
Do you need to flash klipper from the K1 itself or can you use a rasberry pi with klipper installed?

3DCoded, 2024-12-11:
@brentdeacon23

You can use an external Raspberry Pi with Klipper to flash the SKR.

Closed 2024-12-11.

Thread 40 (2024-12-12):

[MCU]: MKS Monster8

Mawe066, 2024-12-12:
### What kind of controller is this?

main MCU (using spare stepper ports on existing MCU)

### Controller name

MKS Monster8

### More information

For the usage in Happy Hare with no exra MCU. All Steppers are inside the existing MCU

3DCoded, 2024-12-12:
Hi @Mawe066 ,

Do you want the last 4 ports to be used for 3MS extruders (E1, E2, E3, and E4)?

Mawe066, 2024-12-12:
Yes, I have an direct drive and 4 feeding extruders

3DCoded, 2024-12-12:
Hello @Mawe066 ,

I have created the configs using the new configuration generator tool (docs coming soon). Here are the configuration files:

[mmu.zip](https://github.com/user-attachments/files/18117653/mmu.zip)

Mawe066, 2024-12-13:
that was quick, thank you!

3DCoded, 2024-12-13:
Hi @Mawe066 ,

I have found an error in the `mmu_hardware.cfg` I generated. Here's the updated one:

[mmu_hardware.cfg.zip](https://github.com/user-attachments/files/18126428/mmu_hardware.cfg.zip)

Mawe066, 2024-12-13:
What was that error? Maybe I already fixed it. I needed a few more parameters to get no errors.

Mawe066, 2024-12-13:
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

Got errors in missing parameters on interpolate and sense resistor. Had to add these

Mawe066, 2024-12-13:
Ah and I forgot to mention, I use 2209 steppers. In your config were 2208. Maybe add a question in the request template for this

3DCoded, 2024-12-13:
Good idea. I've updated the form so future requests will include the driver question.

Closed 2024-12-13.

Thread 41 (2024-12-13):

[MCU]: Add Bigtreetech SKR V1.3

Marcin1415, 2024-12-13:
### What kind of controller is this?

extra MCU (MCU used specifically for the 3MS)

### Controller name

BTT SKR V1.3

### Stepper Driver Type

A4988

### More information

12/24V

3DCoded, 2024-12-14:
Hello @Marcin1415 ,

I have created a config for the BTT SKR v1.3:

[skr13.zip](https://github.com/user-attachments/files/18135610/skr13.zip)

Closed 2024-12-14.

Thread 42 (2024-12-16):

[MCU]: Spider V3

Gabriel121217, 2024-12-16:
### What kind of controller is this?

main MCU (using spare stepper ports on existing MCU)

### Controller name

Fysetc Spider V3

### Stepper Driver Type

TMC2209

### More information

24V power supply
Intended to set up 2 channel MMU

3DCoded, 2024-12-16:
Hi @Gabriel121217 ,

Which motors do you want to be used as 3MS motors?

- X-MOT
- Y-MOT
- Z-MOT
- E1-MOT
- E2-MOT
- E3-MOT

Gabriel121217, 2024-12-16:
Hey, I am using E0 & E3

3DCoded, 2024-12-16:
Hi @Gabriel121217 ,

Here are the configs:

[spider.zip](https://github.com/user-attachments/files/18150762/spider.zip)

Gabriel121217, 2024-12-16:
Thank you so much!

Closed 2024-12-16.

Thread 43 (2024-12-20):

[Bug]: SKR Mini e3 V2 mmu.cfg

brentdeacon23, 2024-12-20:
### What happened?

Trying to run on K1. Error thrown, seems to be related to happy-hare/configurations/MMU_0_3_btt_skr_mini_e3_v2/mmu.cfg

Error:
pin MMU_GEAR_UART_1 is an alias for MMU_GEAR_UART

### Klippy Log

[klippy.log](https://github.com/user-attachments/files/18204622/klippy.log)

3DCoded, 2024-12-20:
Hello @brentdeacon23 ,

I have found the issue in the configuration and fixed it. Please let me know if this works.

Closed 2024-12-23.

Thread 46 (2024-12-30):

[MCU]: RAMPS v1.4

Heisenbertgggg, 2024-12-30:
### What kind of controller is this?

extra MCU (MCU used specifically for the 3MS)

### Controller name

ramps 1.4 com arduino

### Stepper Driver Type

a4988

### More information

using 12v

3DCoded, 2024-12-30:
Hi @Heisenbertgggg ,

Here is the `mmu_hardware.cfg` configuration for the RAMPS v1.4 board:

```
[stepper_mmu_gear]
step_pin : mmu:PF0
dir_pin : mmu:PF1
enable_pin : !mmu:PD7
rotation_distance : 25
microsteps : 16

[stepper_mmu_gear_1]
step_pin : mmu:PF6
dir_pin : !mmu:PF7
enable_pin : !mmu:PF2
rotation_distance : 25
microsteps : 16

[stepper_mmu_gear_2]
step_pin : mmu:PL3
dir_pin : mmu:PL1
enable_pin : !mmu:PK0
rotation_distance : 25
microsteps : 16

[stepper_mmu_gear_3]
step_pin : mmu:PA4
dir_pin : mmu:PA6
enable_pin : !mmu:PA2
rotation_distance : 25
microsteps : 16

[stepper_mmu_gear_4]
step_pin : mmu:PC1
dir_pin : mmu:PC3
enable_pin : !mmu:PC7
rotation_distance : 25
microsteps : 16
```

Closed 2024-12-30.

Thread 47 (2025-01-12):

[MCU]: skr mini e3 v1.2

frawgdog, 2025-01-12:
### What kind of controller is this?

extra MCU (MCU used specifically for the 3MS)

### Controller name

Skr mini e3 v1.2

### Stepper Driver Type

TMC2209

### More information

Also I'm not sure if it's possible but it would be nice if there was a way to integrate more than 1 mmu mcu. I'd like to expand to beyond 4 colors.
Thanks for all your work on this!

3DCoded, 2025-01-12:
Hi @frawgdog ,

You can use any number of mmu MCU's with the 3MS, as long as your Klipper host has enough usb ports. When you submit additional controller requests, just make note if it's your 2nd, 3rd, etc. board.

Here is your `mmu_hardware.cfg`:

```
[stepper_mmu_gear]
step_pin : mmu:PB13
dir_pin : !mmu:PB12
enable_pin : !mmu:PB14
rotation_distance : 25
microsteps : 16

[tmc2209 stepper_mmu_gear]
uart_pin : mmu:PB15
run_current : 0.580
stealthchop_threshold : 999999
interpolate : True
sense_resistor : 0.110

[stepper_mmu_gear_1]
step_pin : mmu:PB10
dir_pin : !mmu:PB2
enable_pin : !mmu:PB11
rotation_distance : 25
microsteps : 16

[tmc2209 stepper_mmu_gear_1]
uart_pin : mmu:PC6
run_current : 0.580
stealthchop_threshold : 999999
interpolate : True
sense_resistor : 0.110

[stepper_mmu_gear_2]
step_pin : mmu:PB0
dir_pin : mmu:PC5
enable_pin : !mmu:PB1
rotation_distance : 25
microsteps : 16

[tmc2209 stepper_mmu_gear_2]
uart_pin : mmu:PC10
run_current : 0.580
stealthchop_threshold : 999999
interpolate : True
sense_resistor : 0.110

[stepper_mmu_gear_3]
step_pin : mmu:PB3
dir_pin : !mmu:PB4
enable_pin : !mmu:PD2
rotation_distance : 25
microsteps : 16

[tmc2209 stepper_mmu_gear_3]
uart_pin : mmu:PC11
run_current : 0.650
stealthchop_threshold : 999999
interpolate : True
sense_resistor : 0.110
```

Closed 2025-01-12.

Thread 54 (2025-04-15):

[MCU]: CNC Shield v3

3DCreator-droid, 2025-04-15:
### What kind of controller is this?

extra MCU (MCU used specifically for the 3MS)

### Controller name

CNC Shield v3

### Stepper Driver Type

A4988

### More information

I already have the mmu_hardware file, but I need the mmu.cfg file.

3DCreator-droid, 2025-04-15:
Sorry, I was just a little confused since it said that the MMU.cfg file had to match the pins in the MMU_hardware.cfg file, and it said open an issue if there wasn't an MMU.cfg file for your board.

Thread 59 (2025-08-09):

[MCU]: Creality 4.2.2

johnkiniston, 2025-08-09:
### What kind of controller is this?

extra MCU (MCU used specifically for the 3MS)

### Controller name

Creality 4.2.2

### Stepper Driver Type

A4988

### More information

Using 12 volt power, intending to use for 4 units.

https://raw.githubusercontent.com/Klipper3d/klipper/refs/heads/master/config/printer-creality-ender3-v2-2020.cfg

3DCoded, 2025-08-09:
Hi @johnkiniston ,

Below if your `mmu_hardware.cfg` for the Creality 4.2.2 board.

```
[stepper_mmu_gear]
step_pin : mmu:PC2
dir_pin : mmu:PB9
enable_pin : !mmu:PC3
rotation_distance : 25
microsteps : 16

[stepper_mmu_gear_1]
step_pin : mmu:PB8
dir_pin : mmu:PB7
enable_pin : !mmu:PC3
rotation_distance : 25
microsteps : 16

[stepper_mmu_gear_2]
step_pin : mmu:PB6
dir_pin : !mmu:PB5
enable_pin : !mmu:PC3
rotation_distance : 25
microsteps : 16

[stepper_mmu_gear_3]
step_pin : mmu:PB4
dir_pin : mmu:PB3
enable_pin : !mmu:PC3
rotation_distance : 25
microsteps : 16
```

Closed 2025-08-09.

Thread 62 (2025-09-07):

[MCU]: SKR Mini E3 V1.2 3MS MMU

kenjesse, 2025-09-07:
### What kind of controller is this?

extra MCU (MCU used specifically for the 3MS)

### Controller name

SKR Mini E3 V1.2

### Stepper Driver Type

TMC2209 UART mode

### More information

Board uses 12VDC or 24VDC

3DCoded, 2025-09-07:
Hi @kenjesse ,

Below is your `mmu_hardware.cfg` gear section. Please follow [these](https://github.com/moggieuk/Happy-Hare/wiki/Quick-Start-3MS#installing-configuration) instructions to install it.

```
[stepper_mmu_gear]
step_pin : mmu:PB13
dir_pin : !mmu:PB12
enable_pin : !mmu:PB14
rotation_distance : 25
microsteps : 16

[tmc2209 stepper_mmu_gear]
uart_pin : mmu:PB15
run_current : 0.580
stealthchop_threshold : 999999
interpolate : True
sense_resistor : 0.110

[stepper_mmu_gear_1]
step_pin : mmu:PB10
dir_pin : !mmu:PB2
enable_pin : !mmu:PB11
rotation_distance : 25
microsteps : 16

[tmc2209 stepper_mmu_gear_1]
uart_pin : mmu:PC6
run_current : 0.580
stealthchop_threshold : 999999
interpolate : True
sense_resistor : 0.110

[stepper_mmu_gear_2]
step_pin : mmu:PB0
dir_pin : mmu:PC5
enable_pin : !mmu:PB1
rotation_distance : 25
microsteps : 16

[tmc2209 stepper_mmu_gear_2]
uart_pin : mmu:PC10
run_current : 0.580
stealthchop_threshold : 999999
interpolate : True
sense_resistor : 0.110

[stepper_mmu_gear_3]
step_pin : mmu:PB3
dir_pin : !mmu:PB4
enable_pin : !mmu:PD2
rotation_distance : 25
microsteps : 16

[tmc2209 stepper_mmu_gear_3]
uart_pin : mmu:PC11
run_current : 0.650
stealthchop_threshold : 999999
interpolate : True
sense_resistor : 0.110
```

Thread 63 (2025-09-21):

[MCU]: SKR Mini E3 V3

Molloy042, 2025-09-21:
### What kind of controller is this?

extra MCU (MCU used specifically for the 3MS)

### Controller name

SKR Mini E3 V3

### Stepper Driver Type

Tmc2209

### More information

I would like to attach 4 filament sensor to it. Would that be possible?  Also I'm installing the CFS cutter block for k1c, would that be compatible with 3ms? Thanks!

3DCoded, 2025-09-21:
Hi @Molloy042 ,

Below is your `mmu_hardware.cfg` gear section:

```
[stepper_mmu_gear]
step_pin : mmu:PB13
dir_pin : !mmu:PB12
enable_pin : !mmu:PB14
rotation_distance : 25
microsteps : 16

[tmc2209 stepper_mmu_gear]
uart_pin : mmu:PC11
tx_pin : mmu:PC10
uart_address : 0
run_current : 0.580
stealthchop_threshold : 999999
interpolate : True
sense_resistor : 0.110

[stepper_mmu_gear_1]
step_pin : mmu:PB10
dir_pin : !mmu:PB2
enable_pin : !mmu:PB11
rotation_distance : 25
microsteps : 16

[tmc2209 stepper_mmu_gear_1]
uart_pin : mmu:PC11
tx_pin : mmu:PC10
uart_address : 2
run_current : 0.580
stealthchop_threshold : 999999
interpolate : True
sense_resistor : 0.110

[stepper_mmu_gear_2]
step_pin : mmu:PB0
dir_pin : mmu:PC5
enable_pin : !mmu:PB1
rotation_distance : 25
microsteps : 16

[tmc2209 stepper_mmu_gear_2]
uart_pin : mmu:PC11
tx_pin : mmu:PC10
uart_address : 1
run_current : 0.580
stealthchop_threshold : 999999
interpolate : True
sense_resistor : 0.110

[stepper_mmu_gear_3]
step_pin : mmu:PB3
dir_pin : !mmu:PB4
enable_pin : !mmu:PD1
rotation_distance : 25
microsteps : 16

[tmc2209 stepper_mmu_gear_3]
uart_pin : mmu:PC11
tx_pin : mmu:PC10
uart_address : 3
run_current : 0.650
interpolate : True
sense_resistor : 0.110
```

To install:

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

For the sensors, you can take a look at the pinout:

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

Then configure your sensor pins as described [here](https://3ms.3dcoded.xyz/instructions/config/#filament-sensors).

A note about the K1 series: Creality ships those with their own modified Klipper and Linux version, so I can't guarantee Happy Hare will run properly on there.

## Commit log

2024-06-22 add bom and configuration
2024-06-30 major updates
    [mk8m3.stl]
2024-07-09 add macros docs
    [mk8m3.stl]
2024-07-10 add images, cleanup sample prints
2024-07-10 add speed benefits to notip.md, add filament sensor info to index.md
2024-07-13 add first print and troubleshooting guides
2024-07-13 add toolchange flowchart
2024-07-14 update notipshaping, begin work on filament sensor docs
2024-07-15 spare stepper plugs docs
2024-07-18 more troubleshooting guides and mroe sample prints
2024-08-06 add button to homepage
2024-08-16 add JS to steppers.md
2024-08-16 remove JS from steppers.md
2024-08-17 zm384: Add config instructions, minirambo: Revise wording, assembly: add ZM384 and Mini RAMBo to list
2024-08-20 assembly: update y-splitter recommentation
2024-08-20 instructions: Update explanations section
    Add more information about controllers, specifying the difference between the two types:
    - External mainboard: standard setup
    - Spare stepper ports (existing mainboard): setup name denoted with "(main MCU)"
    Add more informatino about filament units. Specify more information about alternate extruders.
2024-08-20 instructions: Rephrase updating section for clarity
    Remove misleading instructions that allow restarting Klipper from Mainsail/Fluidd. The terminal is the preferred method for this.
2024-08-21 bom: Add alternative extruder option
    Add alternative dual-drive extruder option from the experimental Dual Drive Extruders for TPU feature
2024-08-22 assembly: Add note for certain printers with internal Klipper
2024-08-24 Add updated documentation for KlipperScreen
2024-08-26 feat: Add experimental endless spool feature
    [local_macros.cfg]
2024-09-03 feat: Add SKR Pico documentation
2024-10-18 manual filament cutter first revision
2024-10-18 filament cutter words
2024-11-06 feat: Begin docoumentation overhaul for HH
    [mk8m3.stl]
2024-12-09 Happy Hare v3.0.1 RELEASE!
    [4ysplitter.stl, bottom-v6.stl, mk8m3.stl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]
2024-12-12 chore: Deploy documentation
    [mk8m3.stl]
2025-03-13 fix deleted docs
    [4ysplitter.stl, bottom-v6.stl, local_macros.cfg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]
2025-03-31 added index.de.md
2025-04-01 Revert "Update config.de.md"
    This reverts commit b7138d6fb03673d6f3e887dc943715736a5e8305.
2025-04-01 Revert "Update bom.de.md"
    This reverts commit 4348da818c8a78505a0331634a5e77c065f427ef.
2025-04-01 Revert "Update assembly.de.md"
    This reverts commit 741b74149ecd232be7942d06adfebb1813838ff8.
2025-04-01 Revert "added index.de.md"
    This reverts commit d7784715dc7204dff11a7292daaff88b2bf1da37.
2025-04-01 Revert "Update instructions.de.md"
    This reverts commit b4f88926fedfb5acc0c85c9926f170632dbc46ee.
2025-04-01 Revert "Update config.de.md"
    This reverts commit a10886f5bfe5b40ce644d061a04961c89dfecbf4.
2025-04-08 feat: Add German translation for compare.md
    Added compare.de.md
2025-07-22 refactor: Deploy documentation
    [mk8m3.stl]
2025-09-20 chore: Deploy documentation Add IF-Cut notice on index.md
2025-09-23 chore: Deploy documentation SKR Pico updates, add controller flashing link to final assembly
2025-09-23 fix SKR Pico menuconfig image
2026-04-14 update canonical link
    [mk8m3.stl]
